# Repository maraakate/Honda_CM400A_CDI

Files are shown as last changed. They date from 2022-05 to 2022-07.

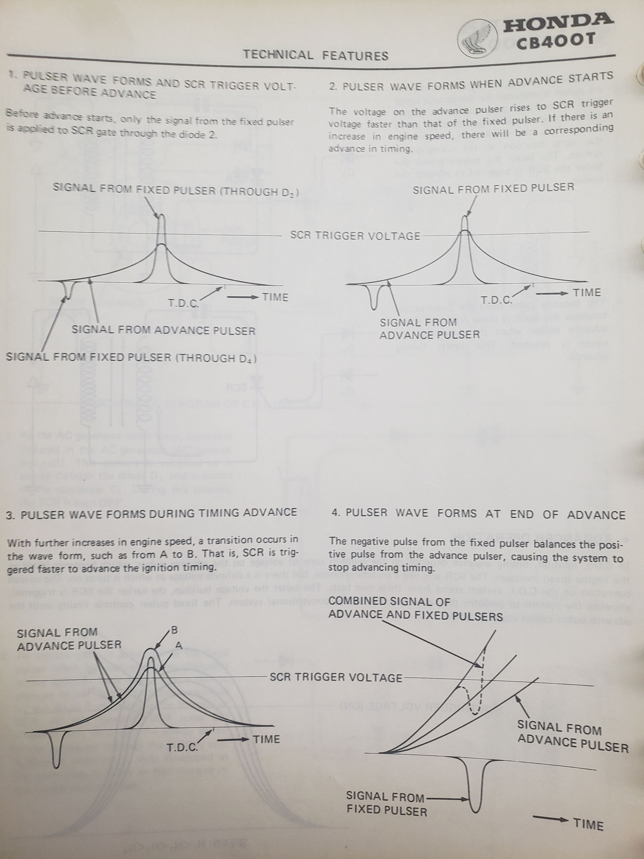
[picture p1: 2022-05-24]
Notes/CB400T_CDI_Theory_4.jpg

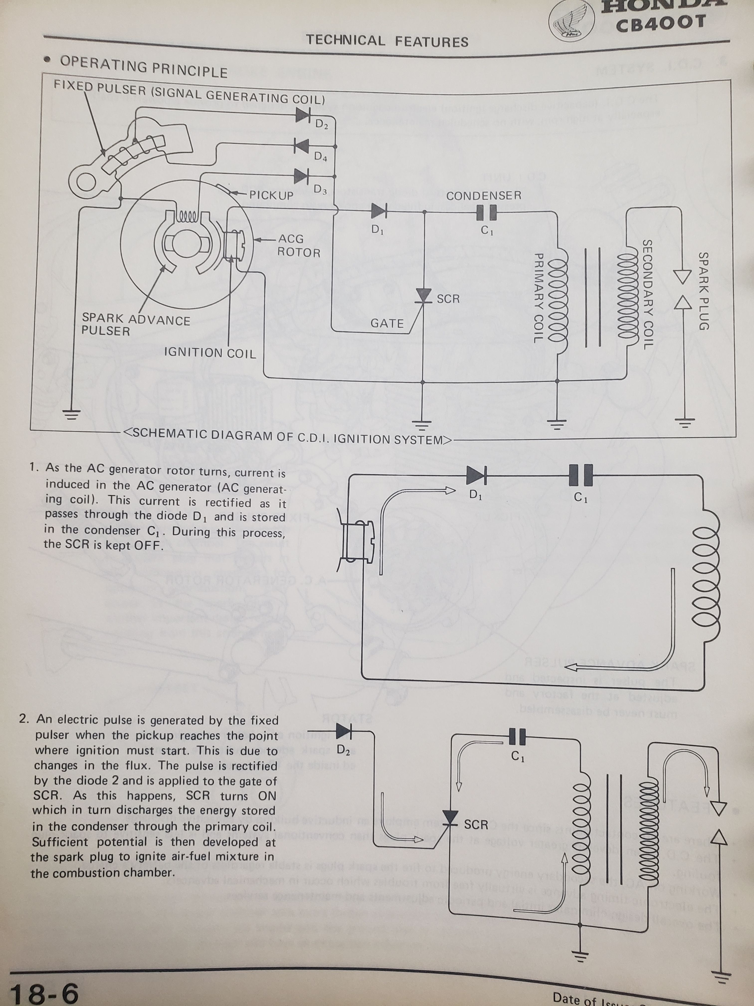
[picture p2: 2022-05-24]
Notes/CB400T_CDI_Theory_2.jpg

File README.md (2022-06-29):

# Honda CM400A CDI and Change Relay
Reverse Engineering of the 1978-1983 Hondamatic CB400A, CM400A and CM450A CDI and Change Relay

Parts list is available in CSV format to export to Digikey. \
Schematic and PCB layout are in KiCAD format.

The original PCB Layout is in PNG format and has layers with an antique \
version of Macromedia Fireworks (it's all I got!).

PCB is now the same dimensions as the original. \
Now in manufacturing phase.   You can pre-order a complete unit \
or purchase a kit at [Hondamatic Parts](https://cm400a.nightgrease.net/)

CDI PCB has been tested and confirmed working: \
https://www.youtube.com/watch?v=neOAnKUinyA \
https://youtube.com/shorts/YKa7PzY36kk

Change Relay schematic has been tested and confirmed working: \
https://youtube.com/shorts/15_SeRSsWy8

For kit builders: \
The following case will mount to the frame from the left mounting \
bolt with a bit of work - https://www.amazon.com/dp/B07TYNYW1S

Grommet for case: \
[7080N16 EPDM Grommet from MCM (7/8" drill hole size x 1 1/8" total length)](https://www.mcmaster.com/catalog/128/4232)

Potting compound: \
[MAX MCR](https://theepoxyexperts.com/product-category/electrical/max-mcr-black-ab/)

Credits: \
Blair M. - Reviewing schematics and lending EE knowledge. \
T. W. Wolfgang - Reviewing schematics and lending EE knowledge. \
Mike B. - Supplying additional broken CDIs, partially completed schematic for CDI. \
Robert L. - Supplying partially completed schematic for Change Relay. \
Steven Myers of [Bearish Cases](https://www.bearishcases.com/) - CAD work for casing. \
PrimesTurmoil - 3D printing. \
Jim and Tom from [VHT](https://vintagehondatwins.com) – Support.

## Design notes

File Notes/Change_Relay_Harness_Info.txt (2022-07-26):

Black - 2" to 2-pin connector (P6)
Red/Green - 2" to 2-pin connector (P7)
Blue/Yellow - 2" to 3-pin connector (P1)
Red/Brown - 2" to 3-pin connector (P2)
Green - 2" to 3-pin connector (P3)
Green/Black - 4" to female bullet (P5)
Light Blue - 4" to male bullet (P4)

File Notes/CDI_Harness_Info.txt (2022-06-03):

11mm PVC sleeving -- approx 2 feet.
6.3mm 2-pin parallel connector for Coil and Change Relay.
18 gauge wire for all -- approx 2.5 feet needed for most.
Green w/ Black tracer is a jumper.

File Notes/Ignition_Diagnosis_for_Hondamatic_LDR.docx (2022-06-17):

Ignition Diagnosis for CB/CM 400/450 Automatic Trans 1978-1983
Original document by Jim O’Brien. Updated by Frank Sapone.

If all these tests are good then the CDI is at fault. Before replacing a CDI all these components have to test good.
Use a Multi-Meter, VOM or Volt-Ohm-Meter, with a new battery and set it to measure electrical resistance in Ohms.
Separate the three connectors from the stator to the CDI for the stator tests, use the stator side connections.
The fuel tank has to be removed to test the coil and run/kill switch. The Black w/White wire pigtail is at the CDI.

Coil Test:

- Primary Side. Measure the resistance between the Yellow and Green wires. The Yellow and Green wires being measured will be coming out of the spark plug coil. The resistance should be less than 1 Ohm. Spec is 0.35 to 0.55 Ohms
- Secondary Side: Measure the resistance of the spark plug wires with the plug end caps removed, they unscrew. Insert a probe into each wire. Spec is 7.2K Ohms to 8.8K Ohms for the stock Honda coil, other coils will have different specs.
- Plug End Caps: Measure the resistance of the plug end caps. Spec is 5K Ohms. Replacement part number is NGK XD05F.

Stator Tests:
The connectors used are found under the left side cover.

- Measure the resistance of the Pink and Green wires in the large 6 pin connector. This is the advance pickup coil. The resistance should be between 10 to 30 Ohms.
- Measure the resistance of the White and Blue wires in the 2 pin connector. This is the power to the CDI. The resistance should be between 4 to 7 Ohms.
- Measure the resistance of the White wire in the 2 pin connector and Green wire in the large 6 pin connector. The resistance should be between 200 to 500 Ohms.
- Measure the resistance of the Brown and Orange wires in the large 6 pin connector. This is the primary pickup coil. The resistance should be between 100 to 200 Ohms.
- The stator ohm readings listed can exceed the old spec by no more than 1 Ohm, more than that will have a negative effect on the timing advance. If unsure after measurement, you should verify with a timing light. At idle in Neutral the timing marks should align to the ‘N’ mark. In 1 or 2 the timing marks should align to the ‘F’ mark. Around ~4000 RPM the timing marks should align somewhere between the double line ‘| |’ marks.

Change Relay Test:

Set your DVM to Volts. Connect the red probe to the Green w/ Red tracer in the 2 pin connector. Connect the black probe to the Green wire in the 3 pin connector. Put the bike on the centerstand and place the bike in Neutral. Turn the key to the “Run” position.

- In Neutral the voltage should be about 0.7V.
- In 1 and 2 the voltage should be 11-13V (should be the same as your battery voltage).

Run/Kill and Ignition switch Tests:

Connect one probe to the Black w/White tracer pigtail wire coming out of the main wiring harness that connects to the CDI unit. Connect the other probe to the negative battery terminal. The results should be:

- Ignition switch on, Run/Kill switch in Run position: Infinite Ohms reading meaning an open circuit.
- Ignition switch on, Run/Kill switch in Off position: 0 Ohms or close to that showing the circuit is closed/completed to ground.
- Ignition switch OFF, Run/Kill in any position: 0 Ohms or close to that showing the circuit is closed/completed to ground.

Alternator Tests: Use the connector with 3 Yellow wires.

Select/connect to one Yellow wire with a probe. Connect the other probe to one of the remaining 2 Yellow wires, resistance should be below 1 Ohm.

Repeat twice using a different wire each time.

If the readings are good then test each of the Yellow wires with one probe connected to ground. There should be an Infinite Ohms reading meaning none of the charging coils is shorted to ground.

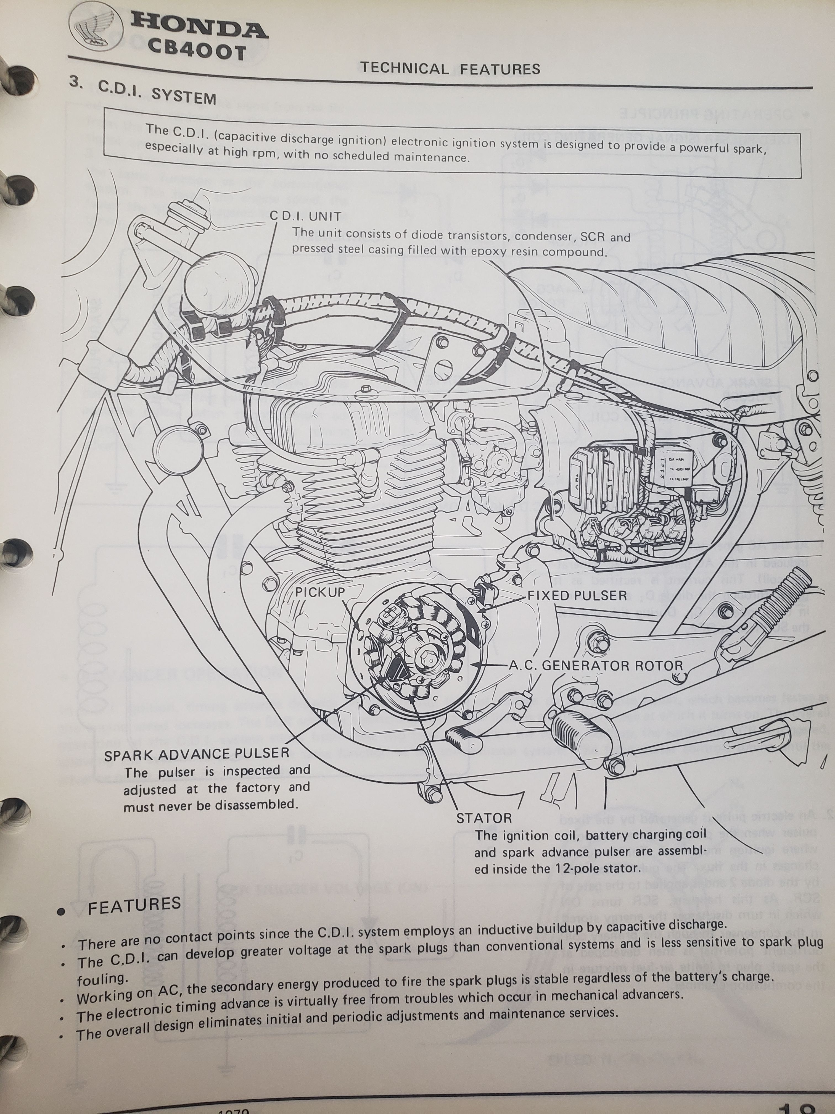
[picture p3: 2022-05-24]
Notes/CB400T_CDI_Theory_1.jpg

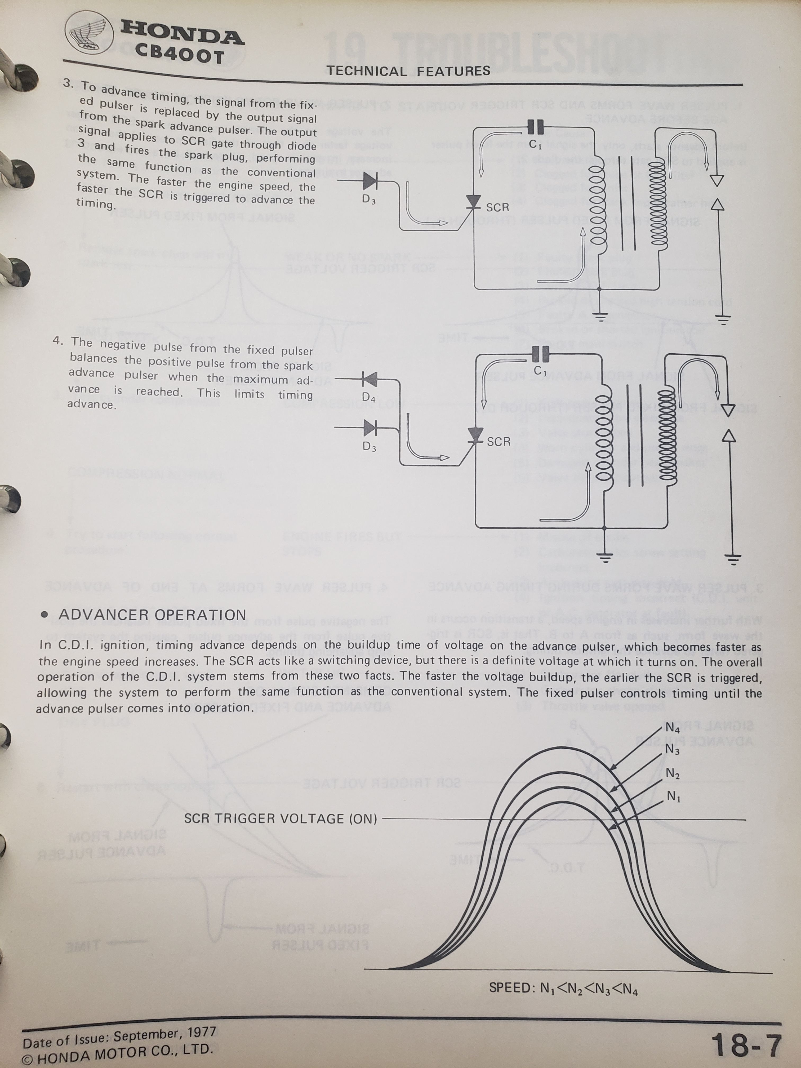
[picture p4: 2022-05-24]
Notes/CB400T_CDI_Theory_3.jpg

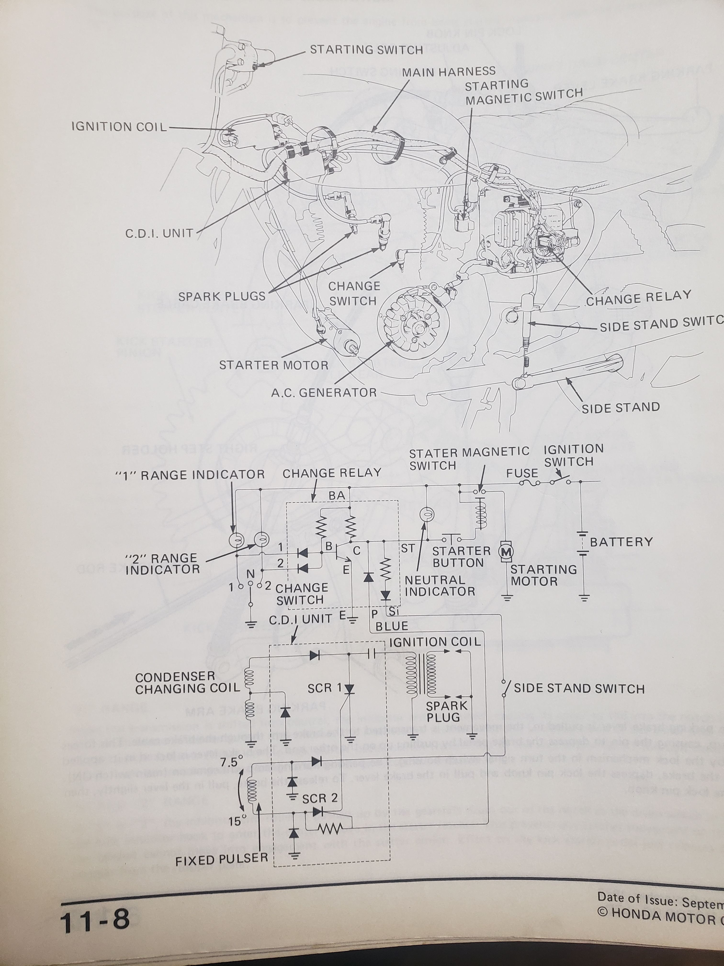
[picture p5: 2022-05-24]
Notes/CB400A_CDI_Theory_2.jpg

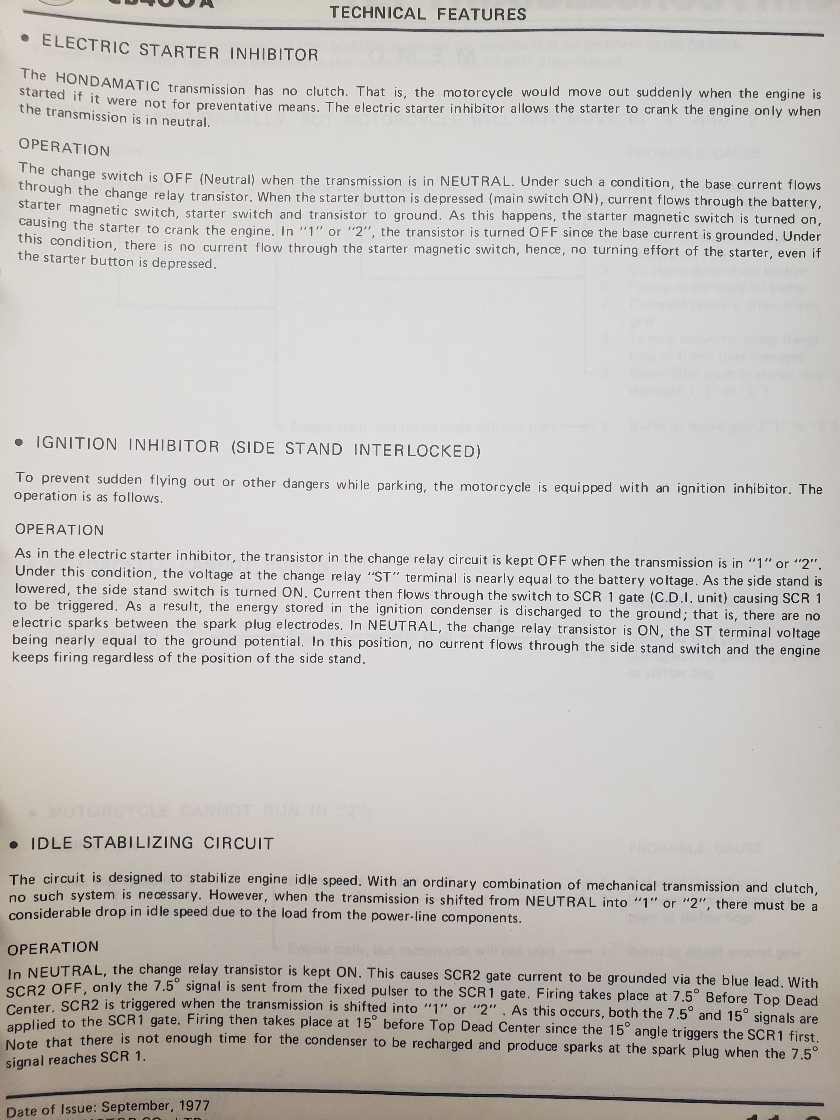
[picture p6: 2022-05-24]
Notes/CB400A_CDI_Theory_1.jpg

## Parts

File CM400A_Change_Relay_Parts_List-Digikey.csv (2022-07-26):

Index | Quantity | Part Number | Manufacturer Part Number | Description | Customer Reference | Available | Backorder | Unit Price | Extended Price USD
1 | 1 | BC3566CT-ND | MBB02070C1001FCT00 | RES 1K OHM 0.6W 1% AXIAL | R1 | 1 | 0 | 0.30000 | 0.30
2 | 1 | BC10.0KZCT-ND | MBB02070C1002FRP00 | RES 10K OHM 0.6W 1% AXIAL | R2 | 1 | 0 | 0.30000 | 0.30
3 | 1 | BC4460CT-ND | MBB02070C3000FCT00 | RES 300 OHM 1% 0.6W AXIAL | R3 | 1 | 0 | 0.29000 | 0.29
4 | 1 | BC249ZCT-ND | MBB02070C2490FRP00 | RES 249 OHM 0.6W 1% AXIAL | R4 | 1 | 0 | 0.30000 | 0.30
5 | 6 | 641-1973-ND | 1N4002B-G | DIODE GEN PURP 100V 1A DO41 | D1-D6 | 6 | 0 | 0.21000 | 1.26
6 | 1 | IRF540NPBF-ND | IRF540NPBF | MOSFET N-CH 100V 33A TO220AB | Q1 | 1 | 0 | 1.35000 | 1.35

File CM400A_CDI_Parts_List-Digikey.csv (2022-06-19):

Index | Quantity | Part Number | Manufacturer Part Number | Description | Customer Reference | Available | Backorder | Unit Price | Extended Price USD
1 | 1 | KC014N-ND | RL2006-125-73-D1 | THERMISTOR NTC 200OHM 3468K DISC | TH1 | 1 | 0 | 2.66000 | 2.66
2 | 1 | KC013N-ND | RL2003-62.4-73-D1 | THERMISTOR NTC 100OHM 3468K DISC | TH2 | 1 | 0 | 3.44000 | 3.44
3 | 2 | 56-SFR25H0004700FR500CT-ND | SFR25H0004700FR500 | RES 470 OHM 1/2W 1% AXIAL | R3, R4 | 2 | 0 | 0.24000 | 0.48
4 | 1 | PPC200W-1CT-ND | PR01000102000JR500 | RES 200 OHM 1W 5% AXIAL | R5 | 1 | 0 | 0.27000 | 0.27
5 | 1 | PPC68W-1CT-ND | PR01000106809JR500 | RES 68 OHM 1W 5% AXIAL | R6 | 1 | 0 | 0.27000 | 0.27
6 | 2 | BC3614CT-ND | MBB02070C1500FCT00 | RES 150 OHM 0.6W 1% AXIAL | R7, R10 | 2 | 0 | 0.30000 | 0.60
7 | 2 | PPC10W-1CT-ND | PR01000101009JR500 | RES 10 OHM 1W 5% AXIAL | R8, R12 | 2 | 0 | 0.27000 | 0.54
8 | 1 | BC3564CT-ND | MBB02070C1000FCT00 | RES 100 OHM 0.6W 1% AXIAL | R11 | 1 | 0 | 0.30000 | 0.30
9 | 4 | 749-2068-1-ND | CCF551K00FKE36 | RES 1 KOHM 1% 1/2W AXIAL | R9, R13, R14, R15 | 4 | 0 | 0.20000 | 0.80
10 | 1 | 399-13043-ND | SMR5104J50J01L16.5CBULK | CAP FILM 0.1UF 5% 50VDC RADIAL | C1 | 1 | 0 | 1.48000 | 1.48
11 | 1 | 493-13019-ND | QAK2G225KTP | CAP FILM 2.2UF 10% 400VDC AXIAL | C2 | 1 | 0 | 4.54000 | 4.54
12 | 8 | 641-1973-ND | 1N4002B-G | DIODE GEN PURP 100V 1A DO41 | D1-D4, D10-13 | 8 | 0 | 0.21000 | 1.68
13 | 5 | 641-1999-ND | 1N4004B-G | DIODE GEN PURP 400V 1A DO41 | D5, D6, D7, D8, D9 | 5 | 0 | 0.21000 | 1.05
14 | 1 | UF5404-E3/54GICT-ND | UF5404-E3/54 | DIODE GEN PURP 400V 3A DO201AD | D14 | 1 | 0 | 0.67000 | 0.67
15 | 1 | 1740-1066-ND | BT151-500R,127 | SCR 500V 12A TO220AB | TR1 | 1 | 0 | 0.66000 | 0.66
16 | 2 | 497-12729-5-ND | TS420-600T | SCR 600V 4A TO220AB | TR2, TR3 | 2 | 0 | 1.42000 | 2.84

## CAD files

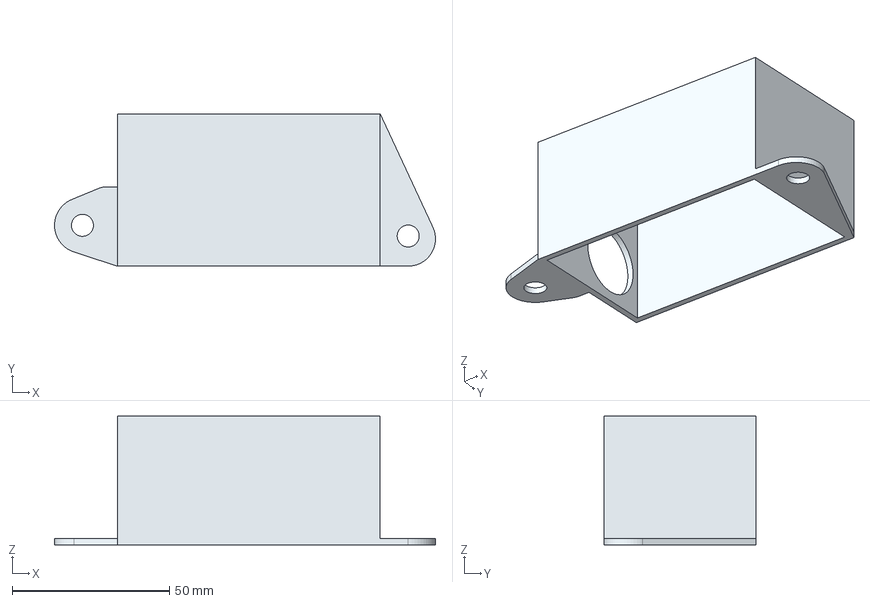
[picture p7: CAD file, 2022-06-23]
Case/cm400a_hondamatic_cdi_housing2.iges
121.3 x 48.5 x 41.0 mm

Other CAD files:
Case/cm400a_hondamatic_cdi_housing2.dwg
Case/cm400a_hondamatic_cdi_housing2.dxf
Case/cm400a_hondamatic_cdi_housing2.stl

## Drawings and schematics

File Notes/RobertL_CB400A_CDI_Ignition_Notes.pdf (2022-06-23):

# Battery

# Kill switch

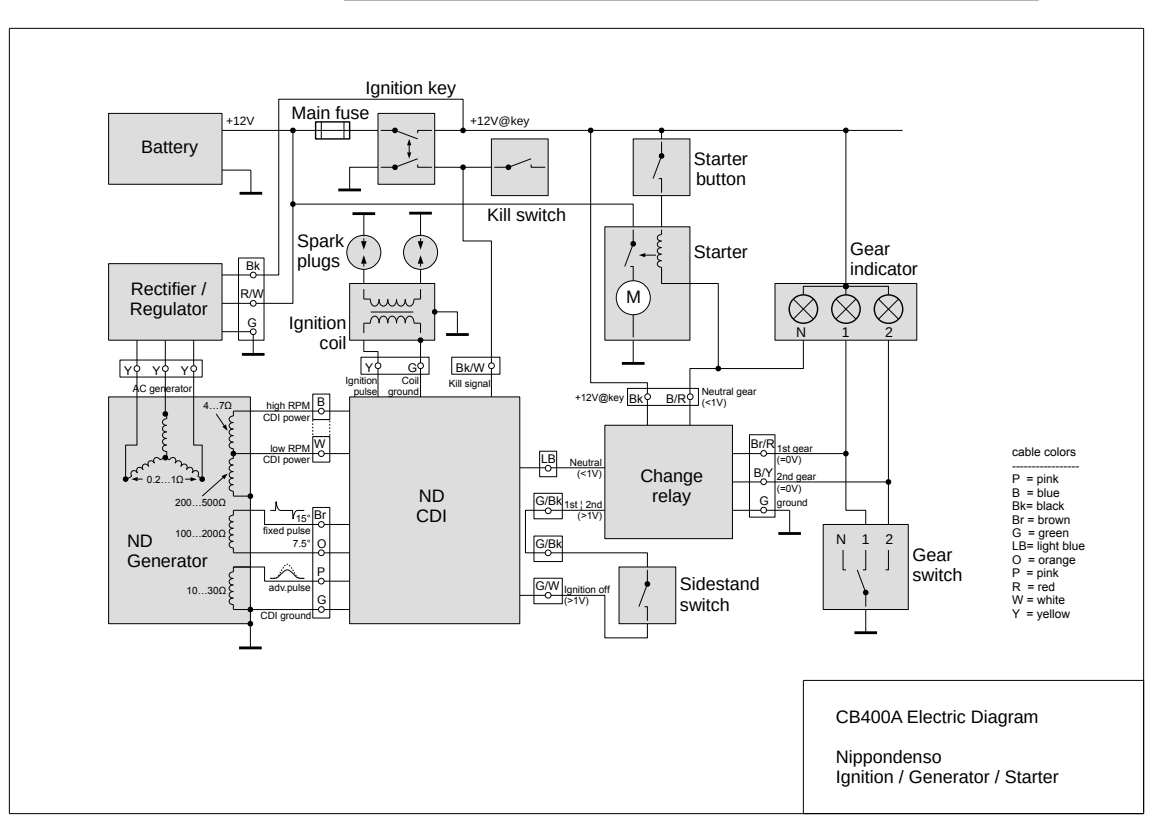
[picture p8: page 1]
CB400A Electric Diagram; ND Generator; ND CDI; Change relay; Rectifier / Regulator; Ignition coil; Sidestand switch; Gear switch; Gear indicator; Starter; Starter button; Spark plugs; cable colors ----------------- P = pink B = blue Bk= black Br = brown G = green LB= light blue O = orange P = pink R = red W = white Y = yellow; low RPM CDI power; high RPM CDI power; CDI ground; adv.pulse; 15° fixed pulse 7.5°; AC generator; Ignition pulse; Kill signal; Neutral (<1V); Ignition off (>1V)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

Nippondenso
Ignition / Generator / Starter

## Nippon-Denso CDI

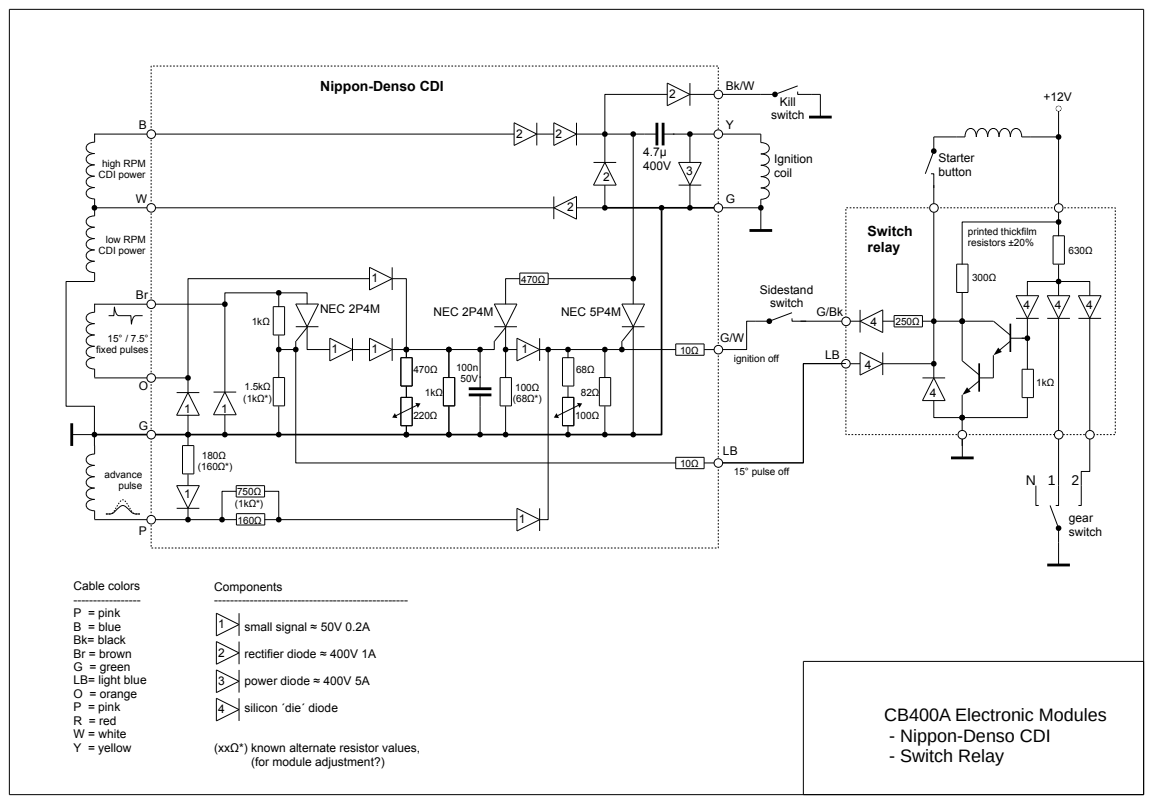
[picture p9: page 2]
NEC 2P4M; NEC 5P4M; Switch relay; Ignition coil; Cable colors ----------------- P = pink B = blue Bk= black Br = brown G = green LB= light blue O = orange P = pink R = red W = white Y = yellow; Components -------------------------------------------------; small signal ≈ 50V 0.2A; rectifier diode ≈ 400V 1A; power diode ≈ 400V 5A; Kill switch; Starter button; Sidestand switch; gear switch; 15° / 7.5° fixed pulses; advance pulse; low RPM CDI power; high RPM CDI power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

silicon ´die´ diode

CB400A Electronic Modules
- Nippon-Denso CDI
- Switch Relay

(xxΩ*) known alternate resistor values,
(for module adjustment?)

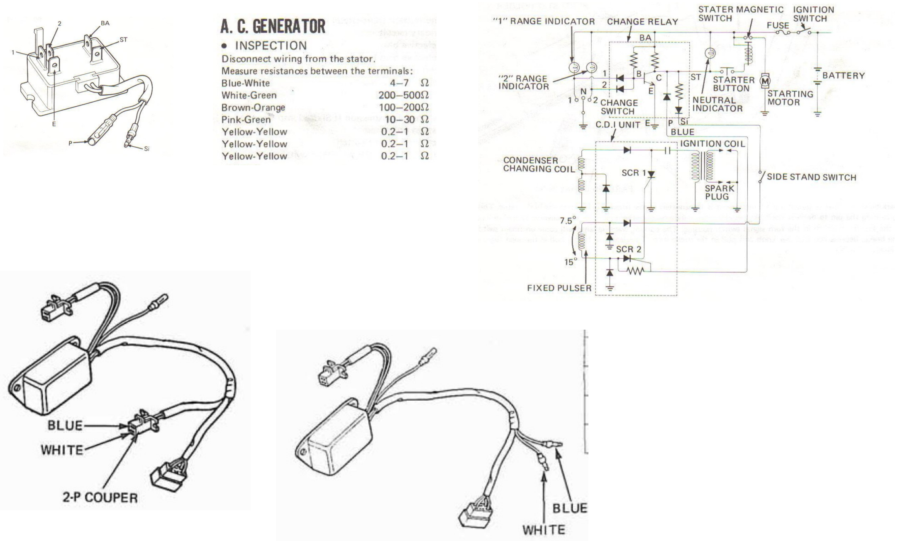
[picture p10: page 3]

Model | CDI | Shift Relay | Ignition Coil | Generator | Comments
Honda part # | Nippondenso | Honda part # | OEM | Honda part # | TEC | Honda part # | Nippondenso
CB400A | 30400-417-004, -014 | 070000-0271 | 38320-417-008 | SH338 | 30530-413-003 | FL102-12V | 31100-417-014 | = Reference components
CM400A/450A | 30400-417-024 | 070000-0550 | | | 30530-447-003 | | 31100-417-024, -034 | similar to CB400A components, but - common 2-pin connector for blue&white wires from generator to CDI - primary input wires of ignition coil on the same side as HV outputs
CB250T | 30400-414-014 | 070000-0261 | -- | -- | 30530-413-003 | FL102-12V | 31100-414-004 | similar to CB400A components, but - no change relay - «7.5°/15°» CDI input wire (light-blue) from change relay removed - «ign.off» CDI wire (green-white) from sidestand switch removed - «7.5° pulse» CDI input wire (orange) from generator removed, corresponding coil connection grounded inside generator - «15° pulse» CDI input wire from generator colored light-blue, instead of brown - 12V charge power specified 130W only, instead of 180W
CB250N | 30400-422-004 | 070000-0420, -0421 | | | | | 31100-442-014, -024 | similar to CB250T components, but - common 2-pin connector for blue&white wires from generator
CM250T | | | | | 30530-447-003 | | | similar to CB250T components, but - common 2-pin connector for blue&white wires from generator - primary input wires of ignition coil on the same side as HV outputs

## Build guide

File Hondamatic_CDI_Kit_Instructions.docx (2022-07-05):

Hondamatic CDI Kit Instructions

Welcome

Thank you for your purchase of the Hondamatic CDI Kit. This kit is applicable to the following bikes: CB400A, CM400A, and CM450A series. It will NOT work for the manual versions of this bike.

Package Contents

Check the package for the following contents:

- Wiring harness.
- CDI Printed Circuit Board (PCB).
- Package of components.

Check the package of components for the following, each bag will be individually labelled:

- C1 Capacitor – 2.2uF @400VDC. Non-polarized.
- C2 Capacitor – 0.1uF @50VDC. Non-polarized.
- TH1 Thermistor – 200 Ohm at room temperature.
- TH2 Thermistor – 100 Ohm at room temperature.
- R3 and R4 Resistors – 470 Ohm.
- R5 Resistor – 200 Ohm.
- R6 Resistor – 68 Ohm.
- R7 and R10 Resistors – 150 Ohm.
- R8 and R12 Resistors – 10 Ohm.
- R11 Resistor – 100 Ohm.
- R9, R13, R14 and R15 Resistors – 1 KOhm.
- D1 through D4, D10 through D13 Diodes (8 total) – 1N4002.
- D5-D9 Diodes (5 total) – 1N4004.
- D14 Diode – 400V 3A.
- TR1 SCR – 500V 12A.
- TR2 and TR3 SCRs – 600V 4A.

If anything is missing, email me fhsapone@gmail.com to get a replacement.

Tools Required

- 25-35W Soldering Iron, or a soldering iron capable of temperature adjustment. DO NOT USE A SOLDERING GUN OR EXTREMELY HIGH WATTAGE IRON. YOU WILL DESTROY THE SCRs AND DIODES!
- Tinner’s such as MG 8342 flux. DO NOT USE ‘PLUMBERS FLUX’.
- Rosin core solder. DO NOT USE ACID CORE/’PLUMBERS SOLDER’.
- Heat gun.
- Wire strippers capable of working with 18-gauge wire.
- Wire cutters.
- Drill with 7/8-inch drill bit for mounting hole of the grommet.
- A case of your choice for mounting the PCB. It’s recommended to use a potting compound rated for electronics once you have verified the unit works. DO NOT USE RTV AS A POTTING COMPOUND.

Pin Assignments

- P1 – Blue.
- P2 – Black with White Tracer.
- P3 – Yellow.
- P4 – Green Coil (two pin connector).
- P5 – Green Harness (six pin connector).
- P6 – White.
- P7 – Orange.
- P8 – Brown.
- P9 – Light Blue.
- P10 – Green with White Tracer.
- P11 – Pink.

Instructions

Working slowly, solder each component individually. You will need to save the large capacitor (C2) for last as it needs to fit over the diodes. Each component corresponds to a number on the circuit board. For example, from the bag labelled R5 there will be R5 labelled on the board. Insert the component in place where it is on the PCB then solder it in place and trim the excess leads with your wire cutters.

Instructions (continued)

The diodes are polarized and must be placed accordingly or you will fry them. There is a white line on the diode and on the PCB. Make sure they line up and the polarity will be correct.

The SCRs also need placed in their proper positions. Pin 1 is always the farthest from the left when looking at the SCR with the numbers (not the backside of the heatsink) facing you. On the PCB you will see square pads where the SCRs go. The square pad is always Pin 1.

The thermistors, SCRs, and C2 also contain heat shrink tubing. This is to prevent them from shorting out other components. For the thermistors, use the smaller tubing on the leads of the component and use your heat gun to shrink it over the leads. Solder the thermistor into place, trim the excess leads, then use the large tubing provided over the entire thermistor and use your heat gun to shrink it over the entire thermistor. For the SCRs, solder the SCR in place, you will have to bend the pins slightly in order to place them on the board. Trim the excess on the leads and place the tubing over the SCR, making sure to cover the metal sink tab. Use your heat gun to shrink it over the entire SCR.

When you have soldered all components and C2 remains there is only one place left for it to go. Use the provided heat shrink tubing to place it on each lead as close to the capacitor as possible and use your heat gun to shrink it over the leads. Solder it into place, as close to the PCB as you can, and trim the leads. For reference, one pad is located to the left of D7 (when viewed from the bottom) and the other is located above the large diode, D14. A picture is attached below, highlighted yellow and circled red for the locations of these pads (board is reversed to show bottom of the board for clarity):

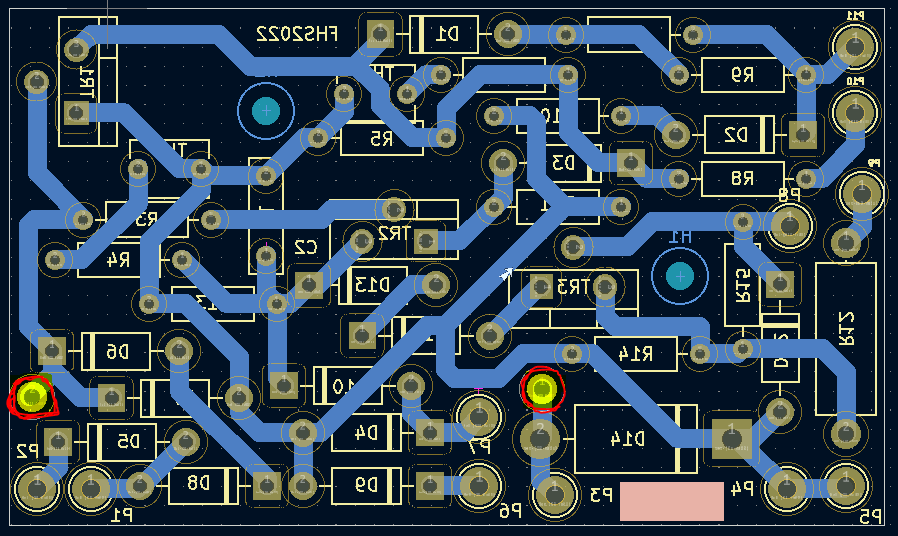
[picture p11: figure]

Instructions (continued)

When you have finished soldering all the components trim back the lengths of the wire on the harness with the side close to the grommet about a quarter inch. Twist the exposed end of the copper and from the top of the PCB feed them through and solder from the bottom.

Now that everything is solder it’s time to double check your work. Pay particular attention to the polarity of the diodes and SCRs. Check the smaller diodes to be sure they are the right kind. If you put the smaller 1N4002s where 1N4004s should be they will fry. Check for any solder blobs/bridging and for any cold solder joints. If you used flux clean the bottom of the PCB with 90% or higher alcohol to remove traces of any flux.

Once you are satisfied that everything is wired up correctly and the board is clean and free of any soldering defects plug it in and go for a ride!

Troubleshooting

If you plug it in and still fail to have spark, check over your work for any kind of soldering defects such as solder blobs/bridging over pads. Correct these defects with a desoldering braid, a desolder bulb, etc. Check to make sure each wire from the harness is in the correct through hole pad on the PCB. Each pad is labelled on the silkscreen. Check that the polarity of the diodes and SCRs are correct. Check that the components are in their right places. If you have found that you have connected something incorrectly and it still does not work after you have corrected it then you likely have fried the SCRs. Email me fhsapone@gmail.com for replacements.

If you are still having issues, you can measure out the board with a DVM. The following page has instructions on how to do this: https://www.vintagehondatwins.com/forums/showthread.php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 . Please take note to use a fresh battery in your DVM to take these readings. If one side is way off, do not panic, reverse the leads and see if it reads correctly. If readings come up incorrect then there is likely a wiring mistake, fried component, or defective component.

If the resistance reading from the CDI comes back good then you likely have a problem with your Stator, Ignition Coil, Change Relay, Ignition Switch or Kill Switch. The following page has instructions on how to test this: https://www.vintagehondatwins.com/forums/showthread.php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 .

If you still have problems and would like to send the CDI back for warranty, please email me fhsapone@gmail.com. For other problems please refer to the Vintage Honda Twins Forums for help at https://www.vintagehondatwins.com/forums .

Credits

This project would not have been successful without the help from the following people:

- Blair M. – Reviewing schematics and lending EE knowledge.
- T. W. Wolfgang – Reviewing schematics and lending EE knowledge.
- Mike B. – Supplying additional broken CDIs, partially completed schematic for CDI.
- Robert L. – Supplying partially completed schematic for Change Relay.
- Steven Myers of Bearish Cases (https://www.bearishcases.com/) – CAD work for casing.
- PrimesTurmoil – 3D printing.
- Jim O’Brien (LongDistanceRider (https://www.vintagehondatwins.com/forums/member.php?4-LongDistanceRider)) and Tom (ancientdad) from VHT (https://www.vintagehondatwins.com/forums/forum.php) – Support.

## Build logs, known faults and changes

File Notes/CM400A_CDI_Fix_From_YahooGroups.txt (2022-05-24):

If you need too fix your old cb400a cdi....heres what worked for
mine
---------------------------------------------------------------------
--
1).replace old capacitor inside with
http://www.mouser.com/Search/ProductDetail.aspx?qs=gb35HGp1gQLzBbm2s
VUZ9A%3d%3d
Manufacturer Part #: 146-400V2.2K
Mouser Part #: 146-400V2.2K
Manufacturer: Xicon
Description: Radial Metallized Polyester Film Capacitors uF 400V
2.2K BLUE

2)replace old scr 3 prong chip labeled 5p4m with this
http://www.mouser.com/Search/ProductDetail.aspx?
qs=JJML70Qc14u1Y7KSFl6
H9Q%3d%3d
otherwise called.. Manufacturer Part #: S4008R
Mouser Part #: 576-S4008R
Manufacturer: Littelfuse
Description: TVS SCR's S4008R

both parts only cost about 2bucks each.
---------------------------------------------------------------------
-------
The haredest thing about this repair is totally removing metal cdi
housing.

Too do this...have a metal worker grind all for corners then peel
and bend
housing off....then throw away. you make a plastic one later.
---------------------------------------------------------------------
-------
Once removed you need too soak the whole cdi but not elec
wire harness-into the strongest jelly type paint stripper from
walmart ($6).
Let soak in small metal can and cover with tin foil maybe a few
hours
until you melt off enough crap to start too see a green or yellow
capacitor.
(THIS CAN SHOCK YOU-dont touch with out insulated tools). If you
can,
see if there are written readable numbers on this part.
If there is, write them down. If those numbers say 2.2uf good.
If they say 1 or 1.5uf, you'll need a different capacitor then the
one I used.
I had to guess because mine said nothing. I choose 2.2uf 400v film
capacitor
because i saw an old honda cx500 twin that used 2.2uf.
Return unit too paint stripper for up to 3 days.
This should melt all compounds off exposing a clean circuit board.
Wash with garden hose pressure spray , then let dry completely.
---------------------------------------------------------------------
------
IF ANY ONE FINDS OUT WHICH CAPACITOR WAS USED ORIGINALLY,PLEASE LET
ME KNOW
1UF 1.5UF 2UF OR 2.2UF AND WHAT VOLTAGE RATING?
EMAIL ME SJSARTWORK@...
---------------------------------------------------------------------
------
Now remove old capacitor(shaped like 2 aaa batteries side by side).
SNIP THE LEADS CONNECTED TO THE CAPACITOR AS CLOSE TO THE CAPACITOR
AS
POSSIBLE. You'll need too rough these 2 prongs up with sandpaper so
you
can solder to them the new capacitor. It doesnt matter which end you
solder
on where.It's non polarized.
---------------------------------------------------------------------
--------
Next remove old 5p4m scr chip. Should be a rectangle green chip
encased in
a clear plastic housing. Its about the size of a dime. Clip the
chip out
with snippers, leaving the 3 prongs in place. NOTE WHICH DIRECTION
THE CHIP
IS IN PLACE SO YOU CAN SOLDER THE NEW ONE IN THE SAME. Too remove
the prongs
, heat up the prongs with solder iron. While hot ,pull one out at a
time
with pliers. If you know how to desolder stuff , thats is obviously
the
correct thing to do here. Once the prongs are out just stick the tip
of your
solder iron in or on each prong hole and heat up a-lot then remove
iron
quickly. That should clear the little holes.....
---------------------------------------------------------------------
-----
Next position the new chip in like the last one and solder in place.
---------------------------------------------------------------------
------
Look at your circuit board and wire connections. If you see any
cracks in
the solders or circuit paths,resolder up those cracks. Clean any
corrosion
that looks obvious. YOUR ALMOST DONE!!!
---------------------------------------------------------------------
------
Its time too test the unit...
First wrap circuit board completely in electric tape. Doesnt need
too be
tight,you'll remove that later. It's just to prevent shocks to you...
Plug everything into bike as it should. Start and run bike. It
should run
like a charm. If so, remove it from bike and BE CAREFUL...THE
CAPACITOR IS
NOW CHARGED!!! Too remove charge...pull off tape and use insulated
screwdriver to ground the 2 capacitor leads together a few times.
If you dont want to do this, just be careful to not touch any part
of the
actual circuit board or capacitor.
---------------------------------------------------------------------
-------
Lastly you need too make or find a durable plastic housing about
the
original size. You should fill half the container with a non
conductive
silicon or potting compound. Settle cdi into this, then fill the
other side
of plastic container so the cdi should be totally encased in this
silicon.
You might need too let dry for up to a week(the rubber helps
protect from
(weather,vibration,and heat). Just be patient, cause you'll have a
working
cdi for real cheap and will have saved possible hundreds. Also youll
have
the gratified feeling of do it youself cdi fix...

good luck
god bless
and be careful
email me and let me know if this helped you sjsartwork@...

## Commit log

2022-05-24 Add current schematic, PCB, notes, etc.
    [CDI_PCB.kicad_pcb, CDI_PCB.kicad_sch, CM400A_CDI_Parts_List-Digikey.csv]
2022-05-26 Shrink board down to 3x3. Flip it so it works with Gerber files so it can be sent off. Back up original design, just in case. (To be removed in the future)
    [CDI_PCB_Original.kicad_pcb]
2022-05-26 Shrink it down another 0.5in
    [CDI_PCB.kicad_pcb]
2022-06-03 Update README.md
    Update README to reflect that the PCB has been tested and confirmed working.
2022-06-03 Shrink the board size down to the original dimensions (69.8mm x 41.4mm) Add Rev3 gerber files as a zip. Add Rev4 gerber files (current version) as a zip. Add notes on making the harness.
    [CDI_PCB.kicad_pcb, CDI_PCB.kicad_sch]
2022-06-10 Add untested Change Switch Relay circuit based on the work of Robert L. Transistor values were unknown, but considering circuit size a 2N3904 should work.
    [Change_Switch_Relay.kicad_pcb, Change_Switch_Relay.kicad_sch]
2022-06-11 Revision 5:
    Remove 'K' on F Silkscreen layer.
    Add mounting two mounting holes in case someone wants it.
    Move TH1 down a bit so TR1 can bend back for room.
    Move Pin 2 of TR2 closer to 1 and 3 to make it a bit easier to add to the board
    [CDI_PCB.kicad_pcb, CDI_PCB.kicad_sch, Change_Switch_Relay.kicad_sch]
2022-06-19 Update parts listing.
    [CM400A_CDI_Parts_List-Digikey.csv]
2022-06-23 Add CAD files for the case.
    [cm400a_hondamatic_cdi_housing2.dwg, cm400a_hondamatic_cdi_housing2.dxf, cm400a_hondamatic_cdi_housing2.iges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]
2022-06-27 Slight change to Rev 5.
    [CDI_PCB.kicad_pcb]
2022-06-28 Change Q1/Q2 to a single IR540NPBF MOSFET. Change R1 to 1K and R2 to 10K.
    [Change_Switch_Relay.kicad_pcb, Change_Switch_Relay.kicad_sch]
2022-06-28 Update README.md
    Update README to reflect current progress, give credit where it is due.
2022-06-29 Shrink Change Relay PCB size down to the original with through hole components.
    [Change_Switch_Relay.kicad_pcb, Change_Switch_Relay.kicad_sch]
2022-07-26 Added Change Relay Parts List.
    [CM400A_Change_Relay_Parts_List-Digikey.csv]
2022-07-26 Add Change Relay Harness/Connector info.
2022-07-26 Add Gerber files for Change Relay Through Hole Revision 1 PCB.
2022-07-26 Re-organize the KICAD files.
    [CDI_PCB.kicad_pcb, CDI_PCB.kicad_sch, CDI_PCB_Prototype.kicad_pcb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]
